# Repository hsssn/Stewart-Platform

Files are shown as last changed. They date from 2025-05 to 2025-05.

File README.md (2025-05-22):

## Stewart-Platform
A servo actuated stewart platform implementation using 3d printed parts and Arduino.

Screenshot (81)

## About
[Stewart Platforms](https://en.wikipedia.org/wiki/Stewart_platform) is a 6DOF parallel manipulator that has its applications in many fields like motion simulation for aircrafts.

# Design
There are various designs with different arrangemetns for the servo motors, most of them work as long as the main principles of the platform are not violated. [This article](https://raw.org/research/inverse-kinematics-of-a-stewart-platform/) shows the possible confugrations, as well as the mathematics behind the linear and rotary actuation. There are also more sources that describe the mathematics, which will be discussed along.
The platform design showed in the implementation is not the best, mechanically, but it works as a first version.

## Parts
- 6 MG995R Servos
- PCA9685 Servo Driver
- Arduino Uno
- Ball Joints
- Metal Rods
- M3 and M4 screws
- 3d printed base and platform, can be found.

## Inverse Kinematics and Maths
For regural platforms using linear actuators, the inverse kinematics process is straight forward vector algebra that calculates the leg lengths needed to reach a specific position and orientation. When adding servo motors, the same lenghts are used and combined with some servo parameters to produce required servo angles. This process is elegantly described in [The Mathematics of The Steart Platform](https://web.archive.org/web/20130506134518/http://www.wokinghamu3a.org.uk/Maths%20of%20the%20Stewart%20Platform%20v5.pdf), and it also describes some basic concepts in robotics like rotation matrices. 

Screenshot (82)

## Code
Before writing the code in Arduino's IDE, it is a good idea to quickly test how everything works. Pyhton was used in this process, and [this repo](https://github.com/Yeok-c/Stewart_Py) by [Yeok-C](https://github.com/Yeok-c) was very helpful in visulaising the result.
The main Arduino code uses [BasicLinearAlgebra](https://github.com/tomstewart89/BasicLinearAlgebra) library, as well as [Adafruit_PWMServoDriver](https://github.com/adafruit/Adafruit-PWM-Servo-Driver-Library) library. It starts by defining base and platform points, as well as servo arm length and rod length. Then, the required leg lengths are calculated, and used to get the servo angles. The angles are then converted to PWMs to write and move the servos. 

## Flaws and Future Improvemets
The flaws in the cureent implementation are mainly mechanical and related to the design, so another iterative design process is required to eleminate them. The main one is the fact that ball joints are not very tight, and they allow for unwanted movement.
This implementation serves as a base for future work. For now, the desired configuration is achieved by hard-coding it, but any input device like joysticks and potentiometers can be added easiely. 
I plan to get inputs from any flight simulation software and use them to move the platform.

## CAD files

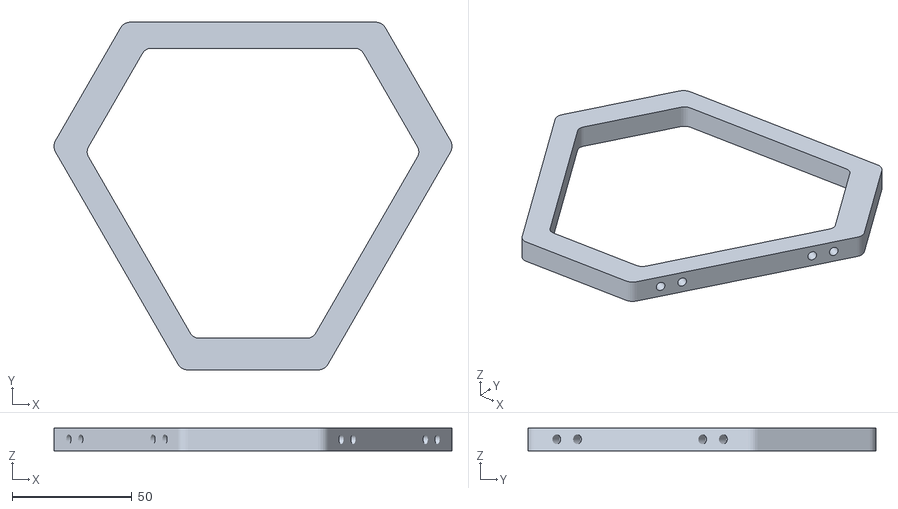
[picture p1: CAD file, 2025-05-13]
Base1.stl
166.5 x 145.5 x 9.60

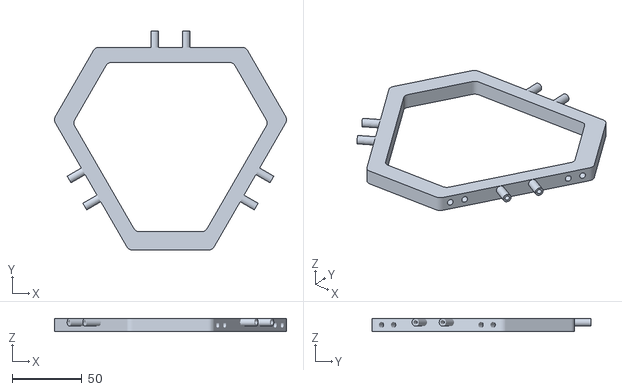
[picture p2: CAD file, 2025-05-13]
Platform.stl
166.5 x 157.2 x 9.60

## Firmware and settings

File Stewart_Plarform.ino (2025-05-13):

#include <Wire.h>
#include <Adafruit_PWMServoDriver.h>
#include <BasicLinearAlgebra.h>
#define SERVOMIN  125 // This is the 'minimum' pulse length count (out of 4096)
#define SERVOMAX  640 // This is the 'maximum' pulse length count (out of 4096)
#define USMIN  600 // This is the rounded 'minimum' microsecond length based on the minimum pulse of 150
#define USMAX  2400 // This is the rounded 'maximum' microsecond length based on the maximum pulse of 600
#define SERVO_FREQ 50 // Analog servos run at ~50 Hz updates]


using namespace BLA;

BLA::Matrix<3,6, double> base_points = {54.108,89.337, 35.228, -35.228, -89.337, -54.108,
                        -71.918, -10.9, 82.817, 82.817, -10.9, -71.918,
                        0,0,0,0,0,0}; // Coordinates of the Base Points based on the design.
BLA::Matrix<3,6, double> platform_points = {61.535, 72.769, 11.228, -11.228, -72.764, -61.535,
                                -48.493, -29.044, 77.537, 77.537, -29.654, -48.493,
                                89,89,89,89,89,89};  // Coordinates of the Platform Points based on the design.

const BLA::Matrix<1,6, double> beta = {PI/3, 7*PI/6, PI, 2*PI, 5*PI/3, 2*PI/3};
BLA::Matrix<1,6, double> z = {0, 0, 0, 0, 0, 0}; // Variable used in calculating angles
const double ldl = 89.0; // Servo Rod length.
const double lhl =  24.0; // Servo arm length                               
const BLA::Matrix<1,3, double> r_angles = {0,0, 0}; // Roll, Pitch, and Yaw angles, specified by the user.
const BLA::Matrix<3,1, double> T = {0,0,0}; // Transformation of the platform, specified by the user.
BLA::Matrix<3,3, double> rotx(double theta); // X-Rotation Matrix.
BLA::Matrix<3,3, double> roty(double psi); // Y-Rotation Matrix.
BLA::Matrix<3,3, double> rotz(double phi); // Z-Rotation Matrix.
BLA::Matrix<1,6, double> calculate_e (BLA::Matrix<3,6, double> l);
BLA::Matrix<3,6, double> calculate_l(BLA::Matrix<3,3, double>r_matrix, BLA::Matrix<3,1,double> T); // Calculate leg lengths.
BLA::Matrix<1,6, double> l_norm(BLA::Matrix<3,6, double> l); // Normalize l.
BLA::Matrix<1,6, double> get_angles (BLA::Matrix<3,6,double> leg_leng, BLA::Matrix<1,6,double> e, BLA::Matrix<1,6, double> gg); // calculate servo angles.
int angleToPulse(int ang); // PWM of Servo angles.

Adafruit_PWMServoDriver pwm = Adafruit_PWMServoDriver(); // Starting the servo driver.

void setup() {

  Serial.begin(9600);
  Serial.println("8 channel Servo test!");

  pwm.begin();
  pwm.setPWMFreq(60);
  
  double ldl_sq = ldl*ldl; // Rod length squared.
  double lhl_sq = lhl*lhl; // Servo arm length squared.
  
  for (int i=0; i < 6; i++){
    
    double aux_0 = platform_points(0,i) - base_points(0,i);
    double aux_0sq = aux_0 * aux_0;
    double aux_1 = platform_points(1,i) - base_points(1,i);
    double aux_1sq = aux_1 * aux_1;
    z(0,i)= sqrt(ldl_sq + lhl_sq - (aux_0sq) - (aux_1sq));
    
    // This block is to calculate z values.
  }
}

void loop() {

  double theta = r_angles(0,0);
  double psi = r_angles(0,1);
  double phi = r_angles(0,2);

  BLA::Matrix<3,3, double> rott = rotx(theta)*roty(psi);
  BLA::Matrix<3,3, double> rotation = rott*rotz(phi);
  BLA::Matrix<3,6, double> leg_leng = calculate_l(rotation, T);
  BLA::Matrix<1,6, double> lll = l_norm(leg_leng);
  
  BLA::Matrix<1,6, double> gg = {0,0,0,0,0,0};
  for (int i =0; i < 6; i++){
    gg(0,i) = lll(0,i)*lll(0,i) - ((ldl*ldl) - (lhl*lhl));
  }
  
  BLA::Matrix<1,6, double> e = {0,0,0,0,0,0};
  for (int i =0; i < 6; i++){
    e(0,i) = 2*lhl*leg_leng(2,i);
  }
  
  BLA::Matrix<1,6, double> angles = get_angles(leg_leng, e, gg);
  Serial.print(angles);
  Serial.println();
  
  for (int j =0; j <5; j++){
    if (j % 2 == 0){
      float ang = angles(0,j) * 180/PI;
      int p = angleToPulse(ang);
      pwm.setPWM(j, 0, p); 
    }
    else {
      float ang = 180 - (angles(0,j)*180/PI);
      int p = angleToPulse(ang);
      pwm.setPWM(j,0,p);     
    }
  }
  
  

}

BLA::Matrix<3,3, double> rotx(double theta){
  BLA::Matrix<3,3, double>rotx = {1,0,0,
                                  0, cos(theta*PI/180), sin(theta*PI/180),
                                  0, -sin(theta*PI/180), cos(theta*PI/180)};
return rotx;
}

BLA::Matrix<3,3, double> roty(double psi){
  BLA::Matrix<3,3, double>roty = {cos(psi*PI/180),0,sin(psi*PI/180),
                                  0, 1, 0,
                                  -sin(psi*PI/180), 0, cos(psi*PI/180)};
return roty;
}

BLA::Matrix<3,3, double> rotz(double phi){
  BLA::Matrix<3,3, double>rotz = {cos(phi*PI/180),-sin(phi*PI/180),0,
                                  sin(phi*PI/180), cos(phi*PI/180), 0,
                                  0, 0, 1};
return rotz;
}

BLA::Matrix<3,6, double> calculate_l(BLA::Matrix<3,3, double>r_matrix, BLA::Matrix<3,1,double> T){

  // Calculates required leg lengths to get to the required configuration, uses basic matrix transformations.
  
  BLA::Matrix<3,6, double> l;
  l.Fill(0);
  BLA::Matrix<3,6, double> aux = r_matrix*platform_points;
  for (int i=0; i < 3; i++){
    for (int j=0; j <6; j++){
      l(i,j) = T(i,0) + aux(i,j) - base_points(i,j);
    }
  }
  return l;
}

BLA::Matrix<1,6, double> l_norm(BLA::Matrix<3,6, double> l){

  // normalizes the leg lengths (using x, y, and z components of each leg).

  BLA::Matrix<1,6, double> norm_l = {0,0,0,0,0,0};
  
  for (int j=0; j <6; j++){
    double sum = 0.0;
    double sum_rt = 0.0;
    for (int i =0; i<3; i++){
      sum = sum + l(i,j)*l(i,j);
    }  
    sum_rt = sqrt(sum);
    norm_l(0,j) = sum_rt;
  }

  return norm_l;
}



BLA::Matrix<1,6, double> calculate_e (BLA::Matrix<3,6, double> l){
  BLA::Matrix<1,6, double> e = {0,0,0,0,0,0};
  for (int i =0; i < 6; i++){
    e(0,i) = 2*lhl*l(2,i);
  }
  return e;
}

BLA::Matrix<1,6, double> get_angles (BLA::Matrix<3,6,double> leg_leng, BLA::Matrix<1,6,double> e, BLA::Matrix<1,6, double> gg) {
  
  // calculate angle values using leg lengths and auxillary variables e and g, the mathematics can be found in the paper linked in the refrences section.
  
  BLA::Matrix<1,6, double> angles = {0,0,0,0,0,0};
  for (int i=0; i < 6; i++){
    double fk = 2* lhl* (cos(beta(0,i))* leg_leng(0,i) + sin(beta(0,i))*leg_leng(1,i));
    double nn = atan2(fk, e(0,i));
    double e_sq = e(0,i)*e(0,i);
    double fk_sq = fk*fk;
    double hh = asin(gg(0,i)/sqrt(e_sq + fk_sq));
    angles(0,i) = hh - nn;
  }
  return angles;
}

int angleToPulse(int ang)                             //gets angle in degree and returns the pulse width
  {  
     int pulse = map(ang,0, 180, SERVOMIN,SERVOMAX);  // map angle of 0 to 180 to Servo min and Servo max 
     // Serial.print("Angle: ");Serial.print(ang);
     // Serial.print(" pulse: ");Serial.println(pulse);
     return pulse;
  }
